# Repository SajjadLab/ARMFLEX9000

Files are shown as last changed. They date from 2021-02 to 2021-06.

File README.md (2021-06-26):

University of British Columbia  
ELEC 391

#### ARMFLEX9000
- Sajjad Al-Kazzaz
- Michael Aono
- Daniel Nadeem

# Quality Control Robot

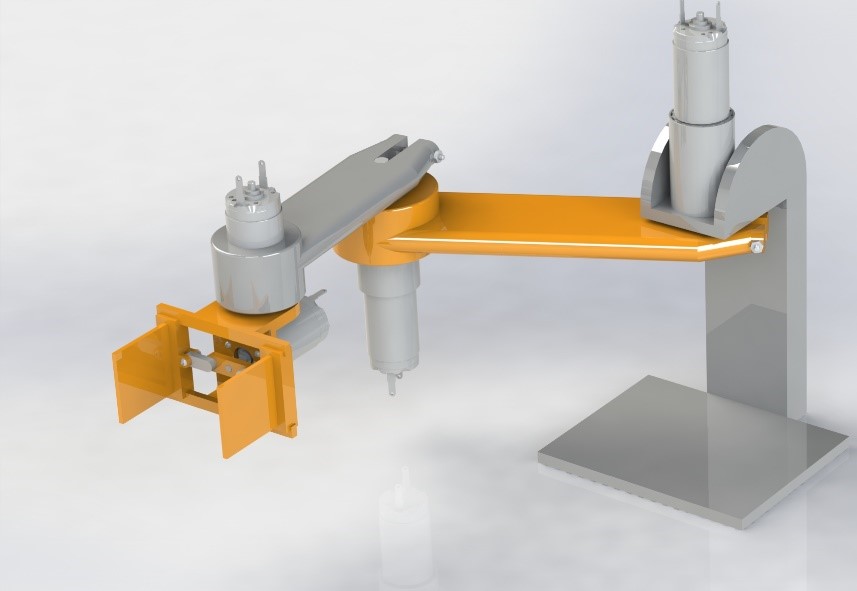
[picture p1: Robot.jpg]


[Project RCG outline](e391Proj2021.pdf)

## Project Details

## Mechanics
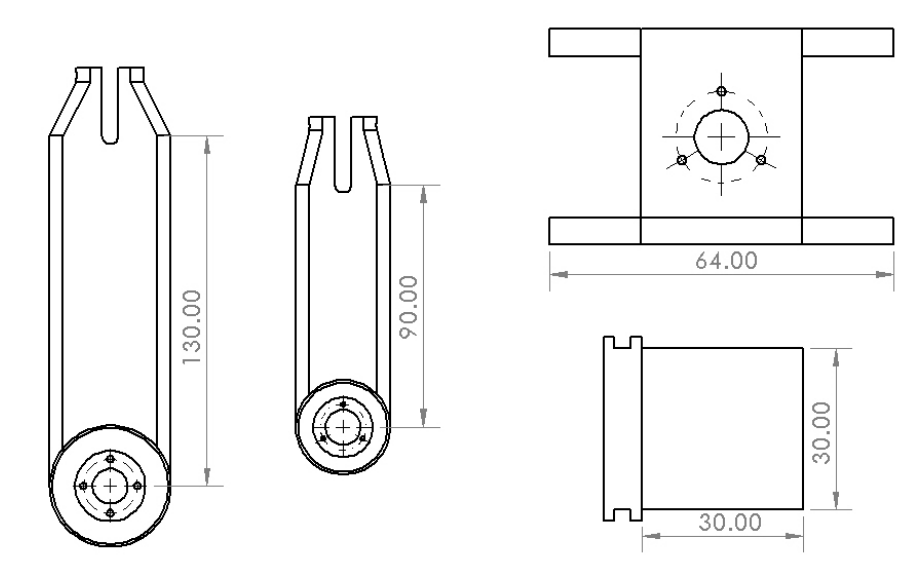
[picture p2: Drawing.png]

The physical model of a series robot arm with an attached gripping mechanism is designed and developed 
to perform quality control on marshmallows. The model is then used to find a linear approximation for 
an operating point, which is in turn used to run a simulation of the quality control procedure.

## Control
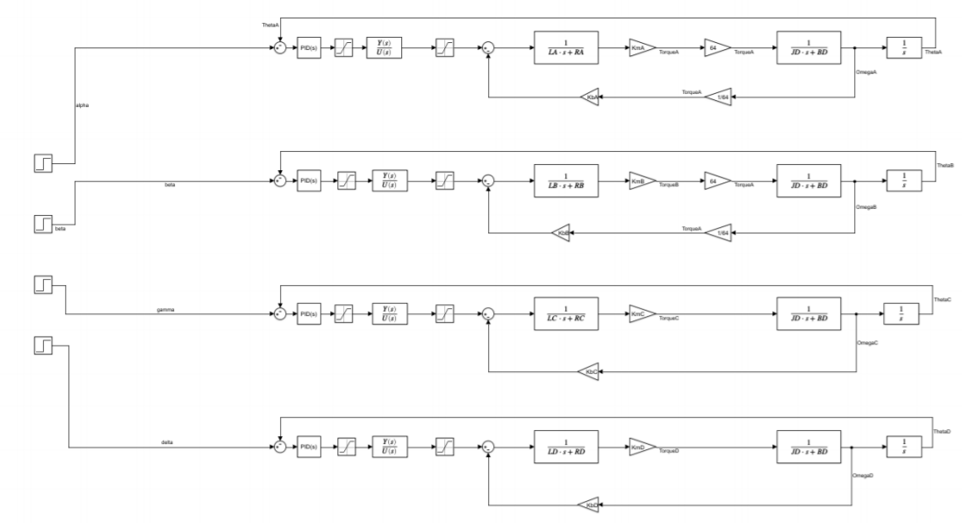
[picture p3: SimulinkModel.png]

ARMFLEX9000 is a 3.5 DOF arm that was developed for the purposes of quality
control of marshmallows on a conveyor-belt. This paper will discuss some aspects
of the design of the robot, as well as control of the robot.

In this paper, Section 1 describes the robotics, including kinematics and path
planning. Section 2 discusses robot modelling in Matlab and SimulationX.
Section 3 describes the Matlab controller, this includes system control and PID
implementation. Section 4 goes over PID tuning. Section 5 describes porting
the controller to C. Finally, Section 6 will discuss system performance.

## Electrical
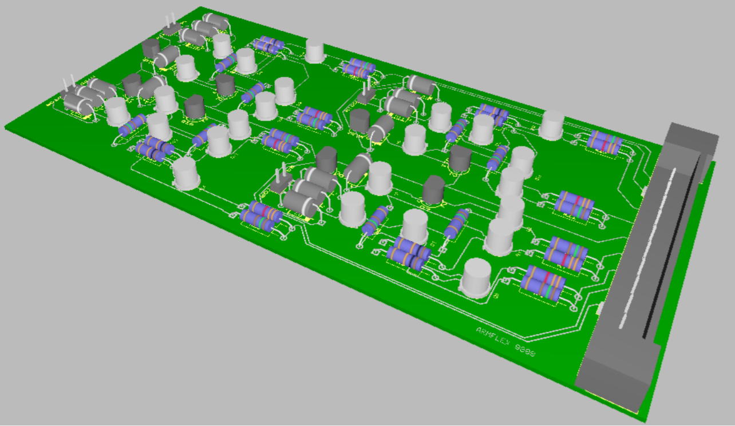
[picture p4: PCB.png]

A driver system is developed to power the motors of the quality control robot. The quality control robot
is capable of three and a half DOF and is powered by 4 identical OTS graphite communicated motors.
The torque requirements of the robot are met with the addition of planetary gear heads of reduction
ratio 64:1 on the base arms. The driver system is of H-bridge form and outputs 11.2V to the motors from
5V input. A PCD design is of the driver is developed to create a mother-daughter board with the Ardinuo
Leonardo.

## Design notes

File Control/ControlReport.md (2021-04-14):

# Quality Control System

## ARMFLEX9000
## April 4, 2021
## Sajjad Al-Kazzaz, ECE, University of British Columbia
## Vancouver, BC, Canada

\newpage

### Table of Contents

- [Abstract](#Abstract)
- [Nomenclature](#Nomenclature)
- [Robotics](#1-robotics)
	- Figure 1.1
- [Modelling](#2-modelling)
- [Controller](#3-controller)
- [Tuning](#4-tuning)
- [Port to C](#5-port-to-c)
- [Performance](#6-performance)

### Abstract

ARMFLEX9000 is a 3.5 DOF arm that was developed for the purposes of quality control of marshmallows on a conveyor-belt. This paper will discuss some aspects of the design of the robot, as well as control of the robot. 

In this paper, Section 1 describes the robotics, including kinematics and path planning. Section 2 discusses robot modelling in Matlab and SimulationX. Section 3 describes the Matlab controller, this includes system control and PID implementation. Section 4 goes over PID tuning. Section 5 describes porting the controller to C. Finally, Section 6 will discuss system performance.

### Nomenclature

- DOF: Degrees of freedom
- PID: Proportional, integral, and derivative

### 1. Robotics

The first thing that had to be done for the robotics of the machine was object placement and path planning. This is a crucial step that determines the length of the arm and thereby the inertia and motors used. The requirements dictated that there should be 3 cylindrical marshmallows on the stopped conveyor which the arm must be able to pick-up and discard. The chosen final positioning was determined with the help of the Mechanical team and optimized for the best results; this positioning is shown in figure 1.1. Given this positioning the optimal arm joint lengths were found to be:

$$r_a = 0.13m$$
$$r_b = 0.09m$$

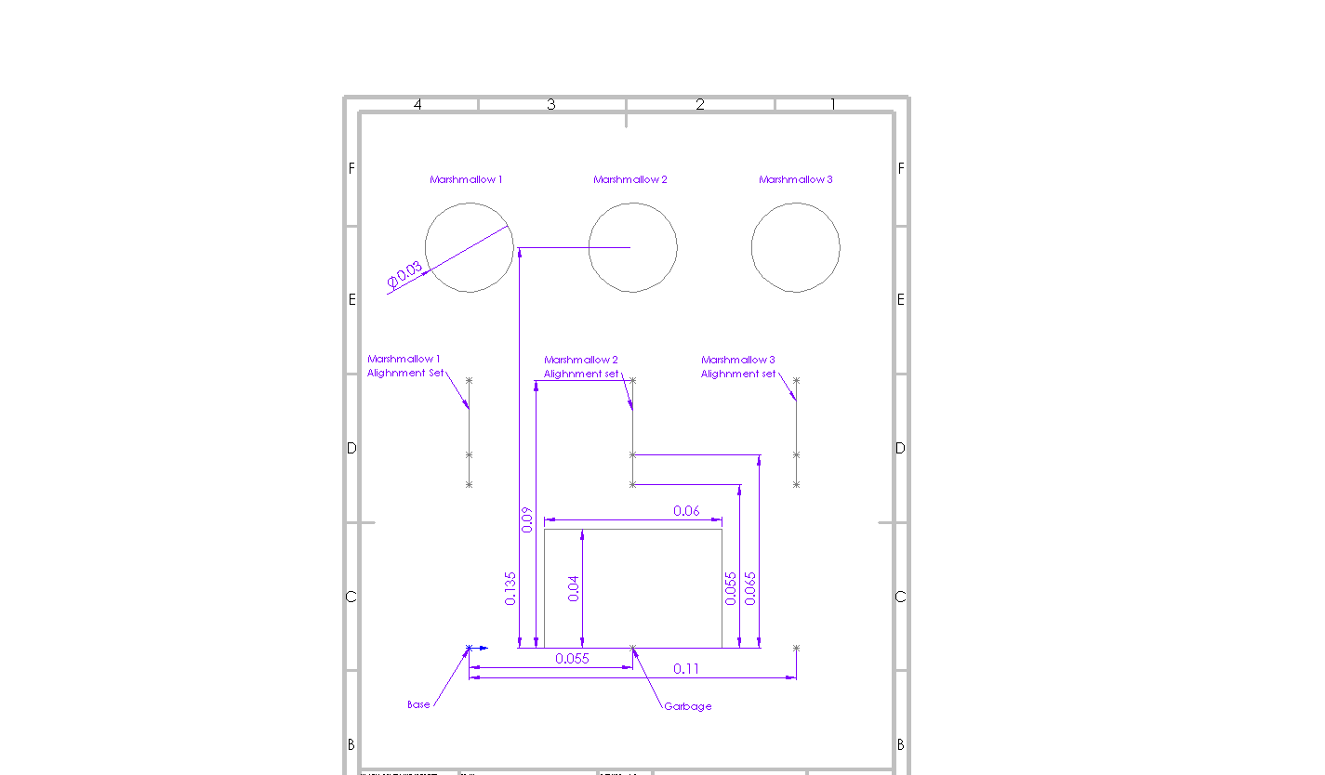
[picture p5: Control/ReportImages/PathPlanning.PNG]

*Figure 1.1*

The dots on figure 1.1 represent the path stage of the arm, to be specific the x and y coordinates of motor C. The arm starts at the calibration stage. The arm then moves to the first alignment dot, also known as the garbage dot. This is so that the arm doesn't swing and knock over marshmallows in its initial movement. The arm then follows a set of alignment dots as it approaches a specific marshmallow so that a general path can be followed that won't knock over or tip other marshmallows. Each marshmallow has its own set of alignment dots shown in the figure by a line that connects said dots. Then the arm will go to the respective pick-up dot to grab the marshmallow, followed by retracing its steps through the alignment dots and then a return to the garbage dot. From the garbage dot the controller will determine whether another marshmallow needs to be grabbed, and follow the outlined stated above, or return home and wait for further commands.

In order to translate the motor C stage coordinates into angles that can be sent to the appropriate motors, a model for inverse kinematics had to be developed. Using trigonometry the position of motor C was translated from the cartesian coordinates of the dots into polar coordinates $\alpha$ and $\beta$ for motors A and B respectively. This was done using the following formulas:

$$\beta = \arccos{\frac{x^2 + y^2 + r_a^2 + r_b^2}{2r_a r_b}}$$
$$\alpha = \arctan{\frac{y}{x}} - \arctan{\frac{r_b \sin{\beta}}{r_a + r_b \cos{\beta}}}$$

To find the necessary angle, $\gamma$, for the swivel motor C so that it remained perpendicular to the conveyor, trigonometry was also used and the following formula was calculated:
$$\gamma = \alpha + \beta - \pi/2$$

Finally, the angle $\delta$ for motor D, which controls the pincher, was found from the design of the pincher to be 0 in the release position, and $\pi/2$ in the grab position. The necessary angle $\delta$ at any time is pre-determined by the stage or dot it is in, and is part of that stages coordinates.

No forward kinematics were used in the controller since the angles were already being calculated and could be used for error calculation. Turning measured angles into measured position was unnecessary and, therefore, removed to save processing time.

### 2. Modelling

Modelling the full system was done using Simulink and SimulationX for the purposes of testing. In Simulink, 4 motor models were developed using the standard motor model and feedback systems as reference. Figure 2.1 shows the 4 motor models, each with its own feedback path. The values for the motors electrical and mechanical components were obtained from the Electrical and Mechanical teams respectively. Using this model as a blueprint, the complete model made for tuning and demoing is shown in Figure 2.2. This model replaces the mechanical components with a communication block connected to SimulationX. SimulationX does the job of more accurately calculating mechanical components and their behaviour during simulation. Figure 2.2 also shows 4 instances of the PID Matlab functions in order to meet requirements, and a central controller (on the far left) that manages overall movement of the system. In SimulationX the Mechanical team developed a simplified model of the arm using the correct weights and lengths for all the components. A Matlab transfer function block is used to model the driver circuit for each of the motors, along with saturation blocks to ensure the voltage limitations of the components aren't exceeded.

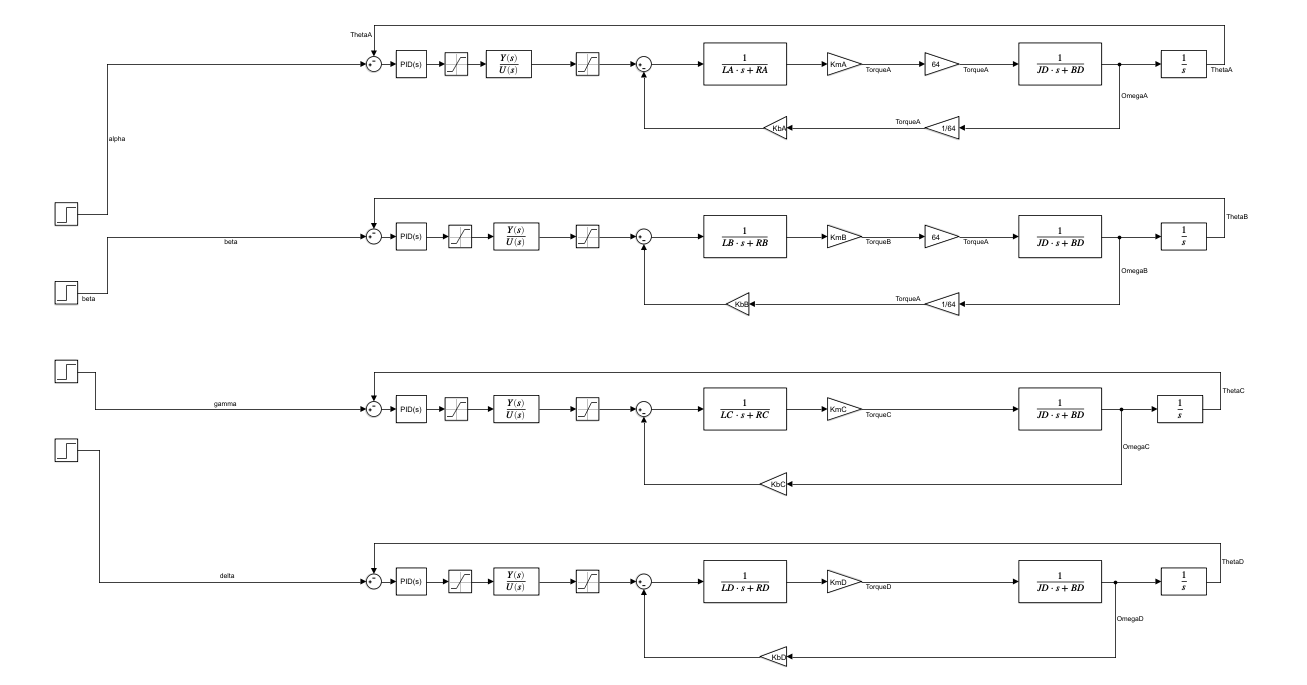
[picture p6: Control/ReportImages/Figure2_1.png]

*Figure 2.1*

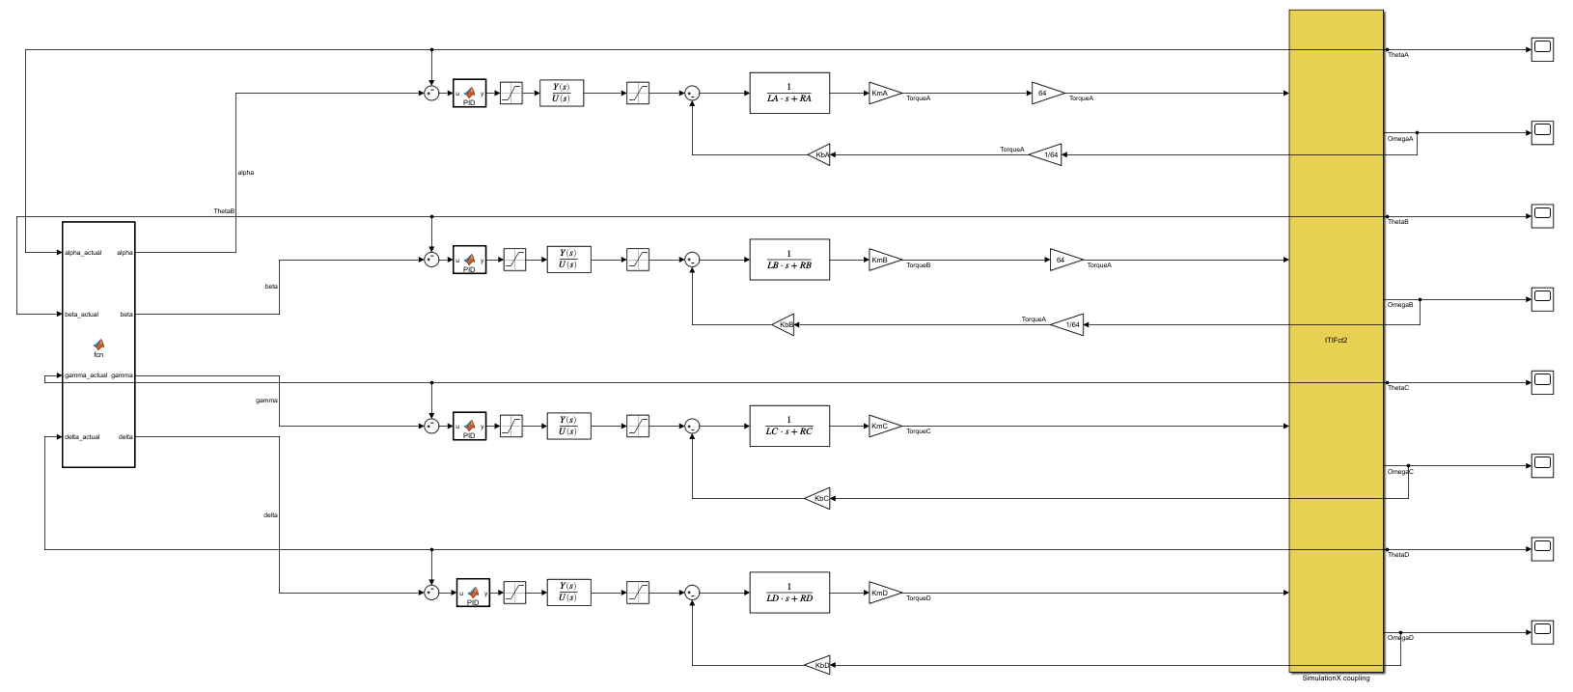
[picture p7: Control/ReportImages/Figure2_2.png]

*Figure 2.2*

### 3. Controller

There are two parts to the system control. The first is the user-defined Matlab function to replace a PID block. Figure 3.1 shows the complete code for the function. Persistent arrays and variables were used to maintain a history of previous error values for the filtered derivative and to keep track of the error sum for the integral output.

```
function y = PID(u)

persistent errorSum
persistent PrevDerivative
persistent ept
persistent Temp
Tsample = 1/500;
nhat = 16;               % Number of samples taken/kept
P = 4/(Tsample*nhat);                 % Pole
KP = 10;
KI = 5;
KD = 2;

% Initialize Temp
if isempty(Temp)
    Temp = 0;
end

% Initialize ept
if isempty(ept)
    ept = zeros(1, nhat);
    total = 0;
    for i = 1:nhat
        calc = P*exp(-P*i*Tsample);
        ept(i) = calc;
        total = total + calc;
    end
    scale = 1/(Tsample*total);
    ept = ept*scale;
end

% Initialize errorSum
if isempty(errorSum)
    errorSum = 0;
end

% Initialize PrevDerivative
if isempty(PrevDerivative)
    PrevDerivative = zeros(1,nhat);
end

% Calculate proportional output
ProportionalOutput = u*KP;

% Calculate integral output
errorSum = errorSum + u*Tsample;
IntegralOutput = errorSum*KI;

% Calculate derivative output
PrevDerivative(1) = (u - Temp);
DerivativeOutput = dot(ept, PrevDerivative)*KD;

% Take a step in time
for n = 1:(nhat - 1)
    PrevDerivative(nhat + 1 - n) = PrevDerivative(nhat - n);
end

% Update Temp
Temp = u;

% Sum all outputs and return,
y = ProportionalOutput + IntegralOutput + DerivativeOutput;
end
```
*Figure 3.1*

The second part of the system control is the system controller. This is a Matlab function that has the coordinates for all the stages relevant to each of the motors and a way of keeping track of which stage the system is in at any point in time. This controller also allows the user to choose which marshmallows to pick-up during the sequence. The complete function is shown in Figure 3.2. Each clock cycle the controller calculates the error between the desired, calculated angles and the true angles being read from SimulationX. Once the error for a particular stage drops below a threshold value, the controller considers that stage complete and increments to the next stage; if the completed stage was the last stage in a marshmallows set then the next marshmallow in the list is targeted. Once the last marshmallow in the list has finished its sequence, the controller sends the arm back to the home calibration position. 

```
function [alpha, beta, gamma, delta] = fcn(alpha_actual, beta_actual, gamma_actual, delta_actual)
% Constants
ra = 0.13;
rb = 0.09;
M1Coord = {[0.055, 0, pi/2], [0, 0.055, 0],     [0, 0.065, 0],     [0, 0.09, 0],     [0, 0.09, pi/2],     [0, 0.065, pi/2],     [0.055, 0, pi/2], [0.055, 0, 0]};
M2Coord = {[0.055, 0, pi/2], [0.055, 0.055, 0], [0.055, 0.065, 0], [0.055, 0.09, 0], [0.055, 0.09, pi/2], [0.055, 0.065, pi/2], [0.055, 0, pi/2], [0.055, 0, 0]};
M3Coord = {[0.055, 0, pi/2], [0.11, 0.055, 0],  [0.11, 0.065, 0],  [0.11, 0.09, 0],  [0.11, 0.09, pi/2],  [0.11, 0.065, pi/2], [0.055, 0, pi/2], [0.055, 0, 0]};
marshmallows = {M1Coord, M2Coord, M3Coord};

% Persistent
persistent completedMarshmallow
persistent completedStage

if isempty(completedMarshmallow)
    completedMarshmallow = 1;
end

if isempty(completedStage)
    completedStage = 1;
end

% Make sure some value exists JIC
alpha = 0;
beta = 0;
gamma = 0;
delta = 0;

% Which and how many marshmallows to grab
marshmallowGrab = [1, 2, 3];
marshmallowCount = 3;

if completedMarshmallow < marshmallowCount + 1
    % If we havent grabbed all the marshmallows then pick
    % completedMarshmallow
    currentMarshmallow = marshmallowGrab(completedMarshmallow);
    
    % Check if we have completed all stages
    if completedStage < 9
        % Set the target position
        xc = marshmallows{currentMarshmallow}{completedStage}(1);
        yc = marshmallows{currentMarshmallow}{completedStage}(2);
        delta = marshmallows{currentMarshmallow}{completedStage}(3);
    
        % Calculate required angles
        beta = acos((xc^2 + yc^2 - ra^2 - rb^2)/(2*ra*rb));

        alpha = atan(yc/xc) - atan((rb*sin(beta))/(ra + rb*cos(beta)));

        gamma = (alpha_actual + beta_actual - pi/2);
        
        % Check if we have reached target location (withing 2%)
        errorAlpha = abs(2*(alpha_actual - alpha)/(abs(alpha_actual) + abs(alpha)))
        errorBeta = abs(2*(beta_actual - beta)/(abs(beta_actual) + abs(beta)))
        errorGamma = (gamma_actual - gamma)
        errorDelta = (delta_actual - delta)
        
        if errorAlpha < 0.02 && errorBeta < 0.02 && errorGamma < 0.002 && errorDelta < 0.005
            % We have reached target position
            % Increment completedStage
            completedStage = completedStage + 1;
        end
    else
        % We have finished all stages so reset and go to next marshmallow
        completedStage = 1;
        completedMarshmallow = completedMarshmallow + 1;
    end
    
else
    % We have grabbed all marshmallow so we return to home
    alpha = 0;
    beta = 0;
    gamma = 0;
    delta = 0;
end

[alpha, beta, gamma, delta];
```
*Figure 3.2*

### 4. Tuning

To tune the system root locus and margin analysis tools were used to give a starting location. The open-loop transfer functions for each of the motors was obtained using the values and models developed in Section 2, Figure 1.2. As an estimation, the value for the controller frequency was chosen to be a very conservative 1000Hz. Thus, nhat, the number of samples used to calculate the filtered derivative, was chosen to be 10; this results in a filter pole of 400 for the purposes of testing. The root locus and margin graphs for the each of the 4 motors are shown in figures 4.1, 4.2, 4.3, and 4.4 respectively. Using this information a suitable starting location for the PID zeros was chosen for each of the motors and tested using the model from Section 2, Figure 1.3. Through trial and error each of the motors were tuned to achieve the desired results. The final PID values for all the motors are summarized in Table 1.1. 

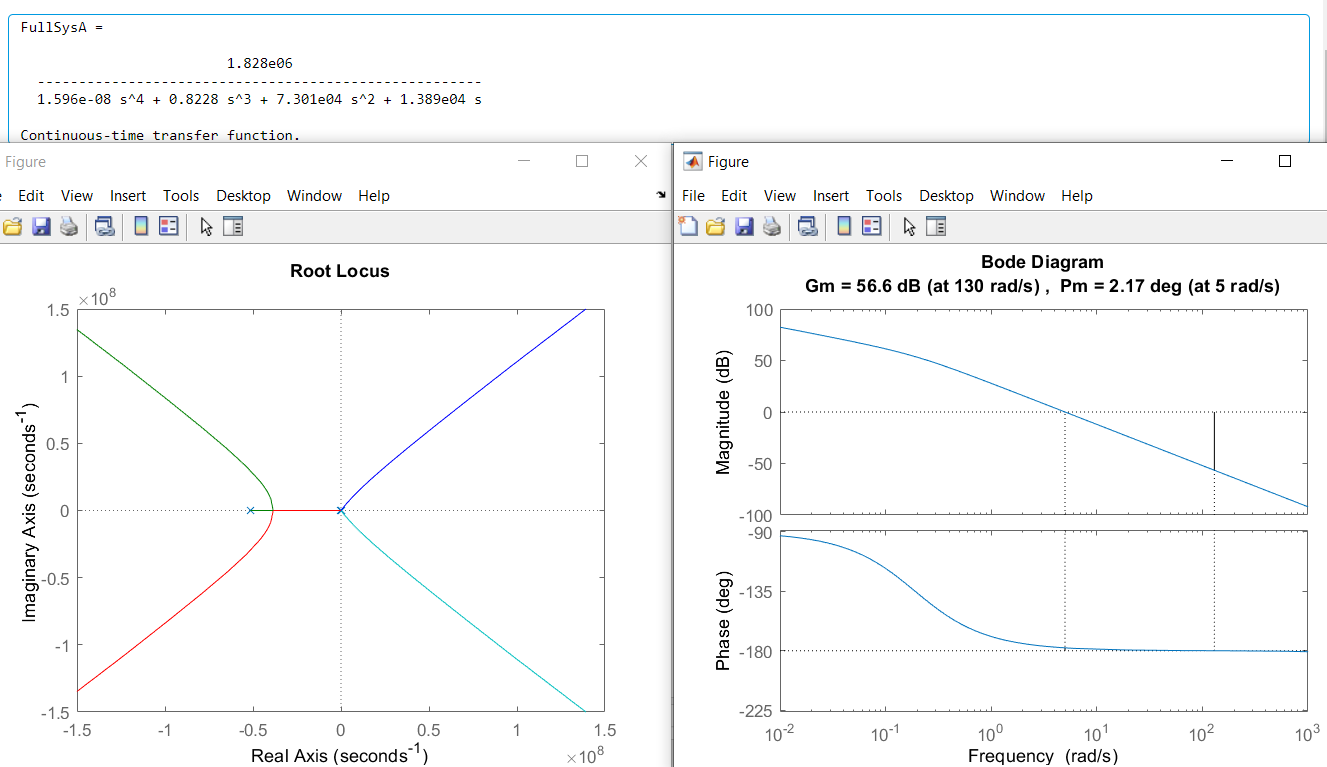
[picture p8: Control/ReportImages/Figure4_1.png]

*Figure 4.1*

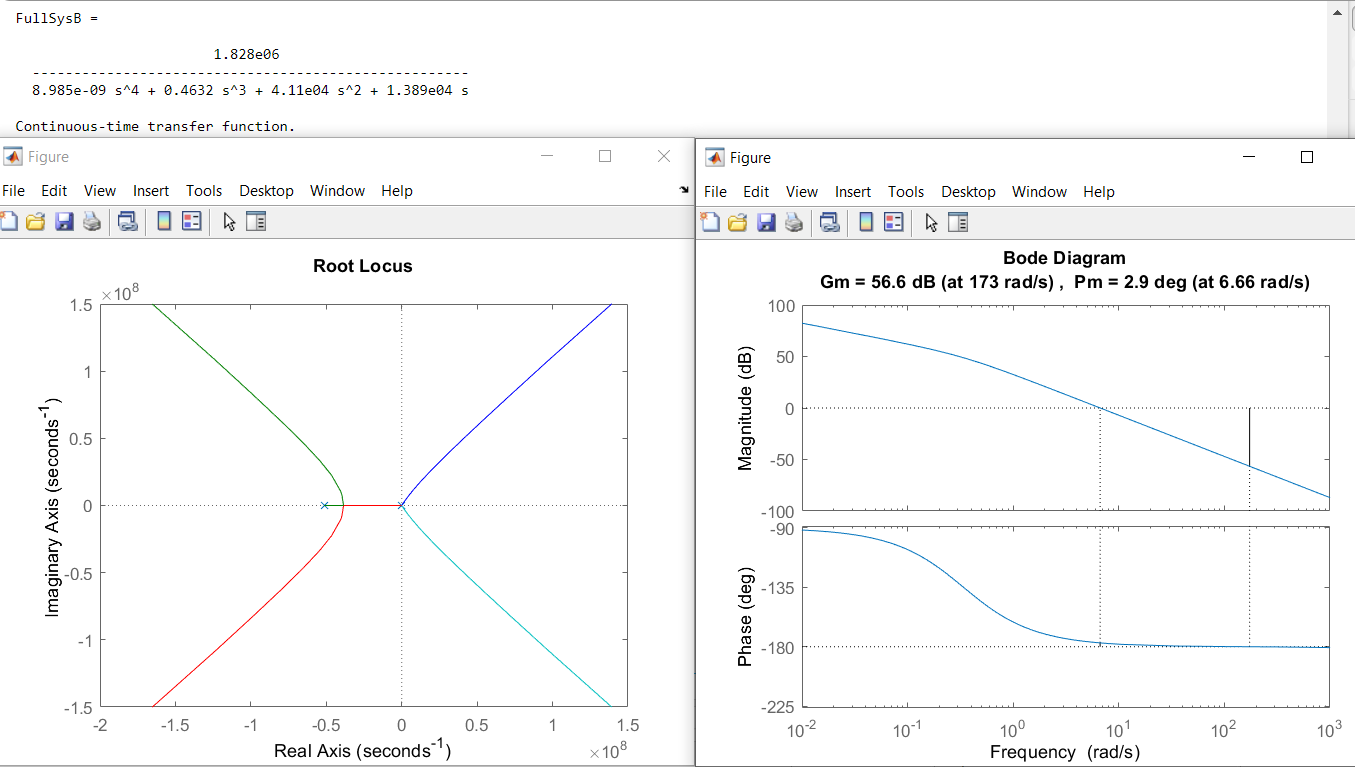
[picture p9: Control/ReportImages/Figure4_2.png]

*Figure 4.2*

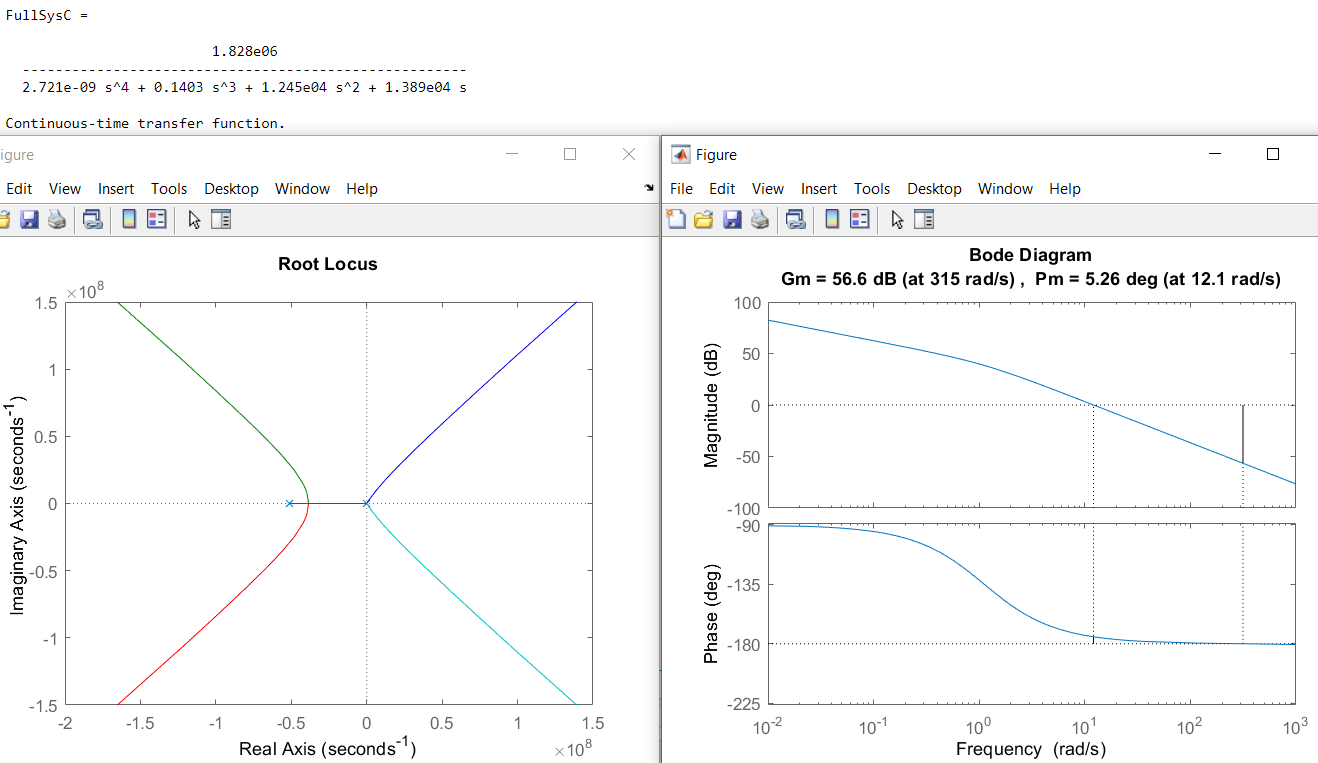
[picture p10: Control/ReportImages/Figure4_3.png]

*Figure 4.3*

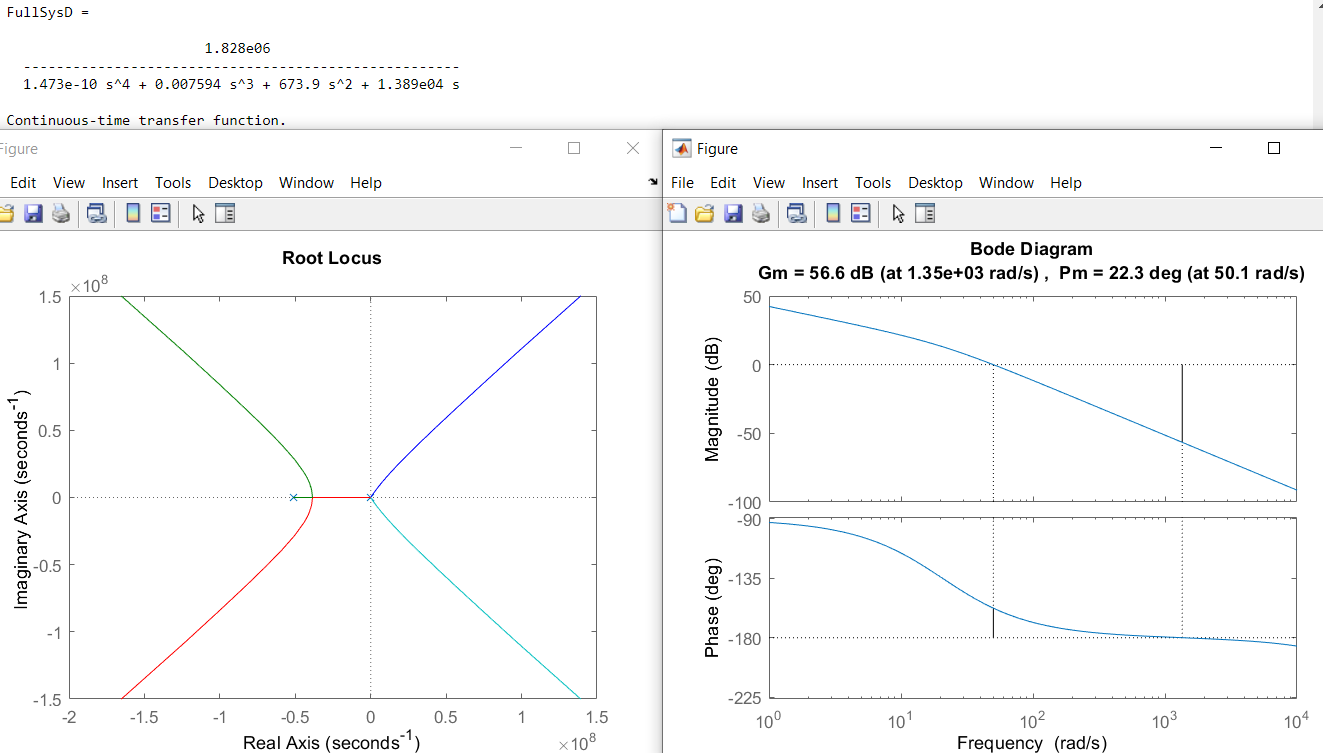
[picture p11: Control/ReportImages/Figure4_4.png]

*Figure 4.4*

*Table 1.1*

### 5. Port to C

Due to the similarities between Matlab and C porting the functions developed in Section 3 was fairly easy. Most of the code was copied straight from the Matlab functions and adjusted to meet the syntax requirements of C. Certain constants, like the arm lengths and their squares, are pre-calculated to reduce processing time. To further save processing time the array of cartesian coordinates for the stages of all the marshmallows are pre-translated to the polar coordinates for $\alpha$ and $\beta$ during setup so that these lengthy calculations aren't repeated during the actual interrupt routine. The complete arduino C code is shown in Figure 5.1.

```
#define TIMER_INTERRUPT_DEBUG 0

// Parameters:
// KP, KI, KD
double gainA[3] = {0.82, 0.008, 0.2};
double gainB[3] = {0.99, 0.01, 0.26};
double gainC[3] = {1, 0.0075, 0.2};
double gainD[3] = {2, 0.1, 0.08};
double ra = 0.13;
double rb = 0.09;
#define RaSquared 0.0169
#define RbSquared 0.0081
#define RaRb2 0.0234   // 2*ra*rb
#define HalfTurn 1.571 // Pi/2

// Timer
#define USE_TIMER_1 true
#define TIMER1_FREQ_HZ 3000

// Libraries
#include <math.h>
#include "TimerInterrupt.h"

const double Tsample = 1/3000;
const int nhat = 8;
const int P = 4/(Tsample*nhat);

// Pins:
int InputA = A1;        // Analog input pin for error
int InputB = A1;
int InputC = A1;
int InputD = A1;

int OutputA = A2;      // Analog output pin for the control signal
int OutputB = A3; 
int OutputC = A4; 
int OutputD = A6; 

// Coordinates:
double marshmallows[][8][3] = {\
{{0.055, 0, 0}, {0, 0.055, 0},     {0, 0.065, 0},     {0, 0.09, 0},     {0, 0.09, HalfTurn},     {0, 0.06, HalfTurn},     {0.055, 0, HalfTurn}, {0.055, 0, 0}}\
, {{0.055, 0, 0}, {0.055, 0.055, 0}, {0.055, 0.065, 0}, {0.055, 0.09, 0}, {0.055, 0.09, HalfTurn}, {0.055, 0.06, HalfTurn}, {0.055, 0, HalfTurn}, {0.055, 0, 0}}\
, {{0.055, 0, 0}, {0.11, 0.055, 0},  {0.11, 0.065, 0},  {0.11, 0.09, 0},  {0.11, 0.09, HalfTurn},  {0.11, 0.065, HalfTurn}, {0.055, 0, HalfTurn}, {0.055, 0, 0}}};

// Persistent:
double PrevDerivativeA[nhat] = {0};
double PrevDerivativeB[nhat] = {0};
double PrevDerivativeC[nhat] = {0};
double PrevDerivativeD[nhat] = {0};
double ept[nhat];
double Temp = 0; 
int completedMarshmallow = 0;
int completedStage = 0;
double errorSumA = 0;
double errorSumB = 0;
double errorSumC = 0;
double errorSumD = 0;

// Functions
void PID(int out, double error, double errorSum, double gain[], double PrevDerivative[]) {
  // Proportional
  double ProportionalOutput = gain[0]*error;

  // Integral
  errorSum += error*Tsample;
  double IntegralOutput = gain[1]*errorSum;

  // Filtered derivative
  PrevDerivative[0] = error - Temp;
  
  // Derivative output
  double DerivativeOutput = 0;
  // Dot product
  for(int n=0; n<nhat; n++) {
    DerivativeOutput += PrevDerivative[n]*ept[n];
  }
  
  // Shift PrevDerivative:
  for(int n=0; n<=nhat-1; n++){
    PrevDerivative[nhat + 1 - n] = PrevDerivative[nhat - n];
  }
  
  // Update Temp
  Temp = error;

  // Output
  analogWrite(out, ProportionalOutput + IntegralOutput + DerivativeOutput*gain[2]);
}

void Controller() {
  // Which and how many marshmallows are we grabbing
  int marshmallowGrab[] = {1, 2, 3};
  int marshmallowCount = 3;

  // Read values
  double alpha_actual = analogRead(InputA);
  double beta_actual = analogRead(InputB);
  double gamma_actual = analogRead(InputC);
  double delta_actual = analogRead(InputD);

  if(completedMarshmallow < marshmallowCount) {
    // If we havent grabbed all the marshmallows then pick
    // completedMarshmallow
    int currentMarshmallow = marshmallowGrab[completedMarshmallow];

    if(completedStage < 8) {
      // Set the target position
      double alpha = marshmallows[currentMarshmallow][completedStage][1];
      double beta = marshmallows[currentMarshmallow][completedStage][2];
      double delta = marshmallows[currentMarshmallow][completedStage][3];

      double gamma = (alpha_actual + beta_actual - HalfTurn);

      // Check if we have reached target location (withing 2%)
      double errorAlpha = (alpha_actual - alpha);
      double errorBeta = (beta_actual - beta);
      double errorGamma = (gamma_actual - gamma);
      double errorDelta = (delta_actual - delta);
      
      if(errorAlpha < 0.05 && errorBeta < 0.05 && errorGamma < 0.002 && errorDelta < 0.005) {
        // We have reached target position
        // Increment completedStage
        completedStage++;
      }
      else {
        PID(OutputA, errorAlpha, errorSumA, gainA, PrevDerivativeA);
        PID(OutputB, errorBeta, errorSumB, gainB, PrevDerivativeB);
        PID(OutputC, errorGamma, errorSumC, gainC, PrevDerivativeC);
        PID(OutputD, errorDelta, errorSumD, gainD, PrevDerivativeD);
      }
    }
    else {
      completedStage = 0;
      completedMarshmallow++;
    } 
  }
  else {
    // We are done grabbing, go home and callobrate
    double alpha = 0;
    double beta = 0;
    double gamma = 0;
    double delta = 0;

    // Check if we have reached target location (withing 2%)
    double errorAlpha = (alpha_actual - alpha);
    double errorBeta = (beta_actual - beta);
    double errorGamma = (gamma_actual - gamma);
    double errorDelta = (delta_actual - delta);

    // Call PID
    PID(OutputA, errorAlpha, errorSumA, gainA, PrevDerivativeA);
    PID(OutputB, errorBeta, errorSumB, gainB, PrevDerivativeB);
    PID(OutputC, errorGamma, errorSumC, gainC, PrevDerivativeC);
    PID(OutputD, errorDelta, errorSumD, gainD, PrevDerivativeD);
  }
}

void setup() {
  pinMode(InputA, INPUT);
  pinMode(InputB, INPUT);
  pinMode(InputC, INPUT);
  pinMode(InputD, INPUT);
  
  pinMode(OutputA, OUTPUT);
  pinMode(OutputB, OUTPUT);
  pinMode(OutputC, OUTPUT);
  pinMode(OutputD, OUTPUT);

  // Initialize ept
  if(ept == NULL) {
    int total = 0;
    for(int i=0; i<=nhat; i++){
      ept[i] = P*exp(-P*i*Tsample);
      total = total + ept[i];
    }
    for(int i=0; i<=nhat; i++){
      ept[i] = ept[i]*(1/(Tsample*total))*Tsample;  // Double check
    }
  }

  // Convert to polar
  // For each marshmallow
  for(int i=0; i<3;i++){
    // For each stage
    for(int j=0; j<8;j++){
      double xc = marshmallows[i][j][1];
      double yc = marshmallows[i][j][2];

      // Calculate required angles
      double beta = acos((pow(xc, 2) + pow(yc, 2) - RaSquared - RbSquared)/(RaRb2));

      double alpha = atan(yc/xc) - atan((rb*sin(beta))/(ra + rb*cos(beta)));

      // Replace xc and yc with alpha and beta
      marshmallows[i][j][1] = alpha;
      marshmallows[i][j][2] = beta;
    }
  }
  
  // Initialize interrupt on timer1
  ITimer1.init();
  if (ITimer1.attachInterrupt(TIMER1_FREQ_HZ, Controller))
    Serial.println("Starting  ITimer0 OK, millis() = " + String(millis()));
  else
    Serial.println("Can't set ITimer0. Select another freq. or timer");
}

void loop() {
}
```
*Figure 5.1*

### 6. Performance

The overall arm performance is very fast; in order to pick up all three marshmallows requires just over 10s, picking up any 2 marshmallows requires 7.5s, and picking up just one marshmallow takes 5s. Assuming the probability that any one marshmallow needs to be discarded is 50%, then the expected run time of the arm is 5.94s. Even with the speed the arm moves at there is no overshoot or tipping of any marshmallows.

The processing time of the ISR routine was calculated from the arduino code in Section 5 using the standard clock rates provided. The ISR requires 2207 clock cycles to run. The Leonardo has a clock speed of 16Mhz, therefore, after the controller can run at a maximum of 7250Hz. However, to account for possible delays and errors the controller frequency is set to 7250/2 ~ 3600Hz. The only cost involved in this part of the project is that of the arduino itself which is about $25.

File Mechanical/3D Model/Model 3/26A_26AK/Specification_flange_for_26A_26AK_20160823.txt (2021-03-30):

Gearhead 26/A requires also a specific flange, as per combination with following motors:

2232U...SR
please add 3D - file name: 26A_flange_a

(c) Copyright 2019, DR.FRITZ FAULHABER GMBH & CO.KG.
All rights reserved.

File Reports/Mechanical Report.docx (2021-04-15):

# Quality Control Robot - Mechanics

April 14, 2021

Daniel Nadeem, ECE, UBC, Vancouver, BC, Canada

Abstract

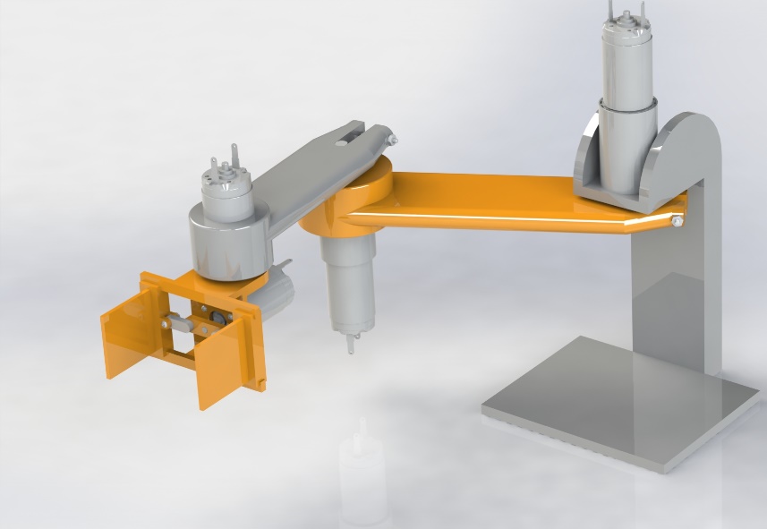
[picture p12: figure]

The physical model of a series robot arm with an attached gripping mechanism is designed and developed to perform quality control on marshmallows. The model is then used to find a linear approximation for an operating point, which is in turn used to run a simulation of the quality control procedure.

Figure 1: Quality Control Robot

The physical model development and analysis is as follows; Section 1 describes the 3D design of the robot including manufacturability. Section 2 describes the method in which the linear model was approximated. Section 3 goes through the stress analysis for determining possible failing points of the robot. Section 4 describes the SimulationX model including methods used to optimize simulation time.

1. 3D Design

The physical model consists of two arm segments, a wrist joint, and a linear gripping mechanism, totaling to 3.5 degrees of freedom. The first and second arm segments are 130mm and 90mm in length, respectively. The gripper claws are square with side lengths of 30mm to match the approximate size of each marshmallow. This can be seen in Figure 2.

All off-the-shelf components come from either the Faulhaber or McMaster-Carr catalogues. These components include four motor/encoder combinations, two of which contain gearheads. As well, fasteners including nuts and bolts are used to secure the robot’s parts together. The remaining custom parts can be 3D printed from ABS plastic. These parts include the first and second arm segments, the gripper base, the two claws, and the gripping linkages.

The robot’s mounting post is designed to route wires up from the base plate, to each of the four motors along the length of the arm. The base plate serves as a housing for the electronics since the space directly above it does not conflict with the path of the robot.


Figure 2: Custom ABS Parts

2. Linear Model

The linear model of the robot is determined using the Mass Properties tool in SolidWorks. The moment of inertia for each of the three motors that control the arm movement, is found by removing the preceding components, then placing the axis of rotation at the origin, and then analyzing the mass properties. For example, the linear model for the second arm motor was found as follows:

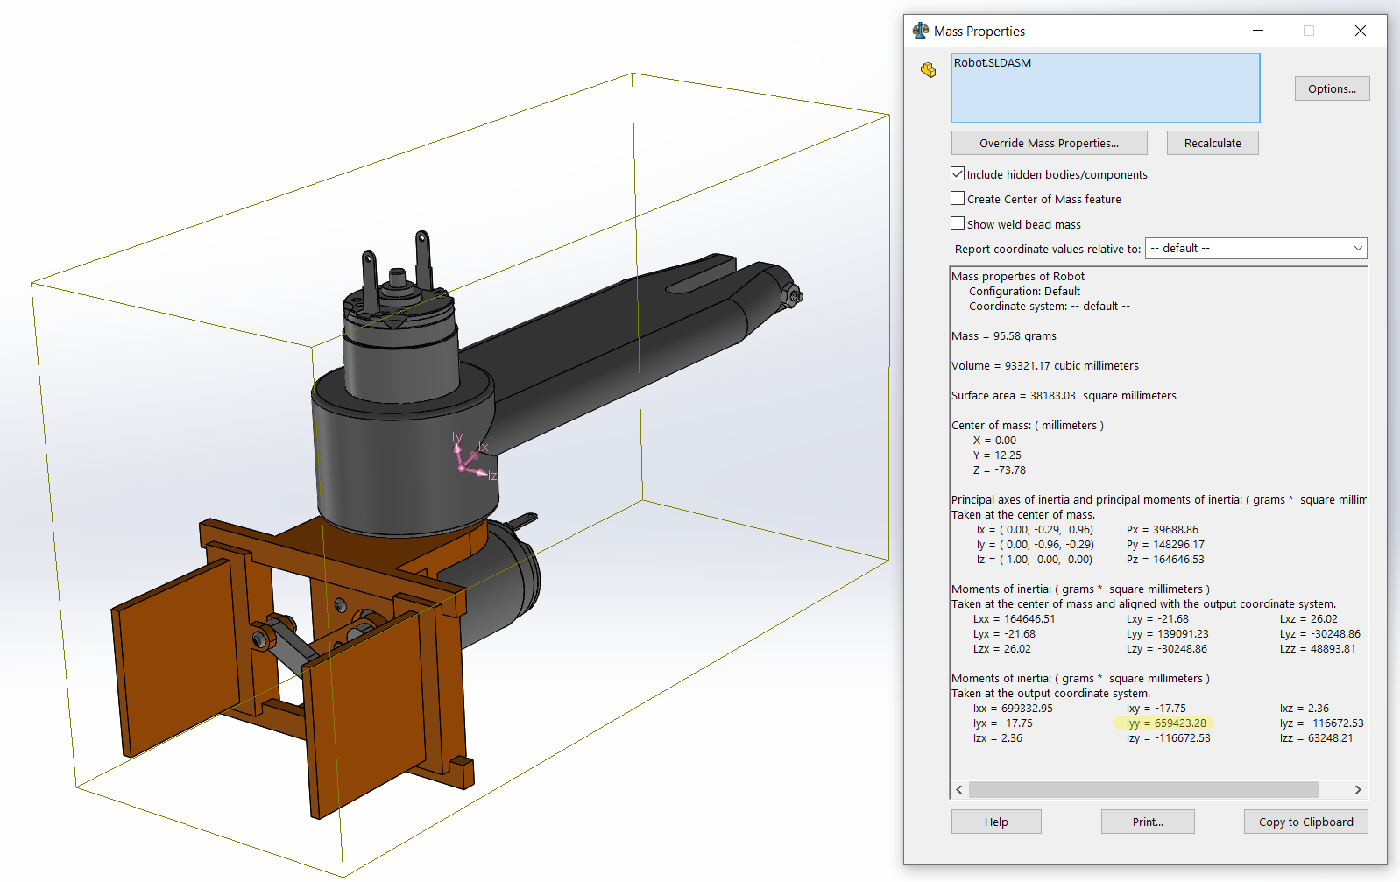
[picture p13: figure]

Figure 3: Mass Analysis

The moment of inertia experienced by the second motor is 0.659 g∙m^2 which is the inertia about the y-axis; the axis of rotation of the second motor. The value for rotational friction is taken from the datasheet of the motor.

3. Stress Analysis

To prevent any failure of the robot’s components in practice, the likely points of stress undergo a simulated test. Of the two arm segments, the maximum potential torque of the motor/gearhead combinations will occur from the second motor as it has the least inertia to move. Of the gripping mechanism parts, the maximum potential force will occur against the claws.

Depicted below are stress tests of the above-mentioned components. In both cases of maximum stress, neither part reaches the breaking point of ABS plastic.

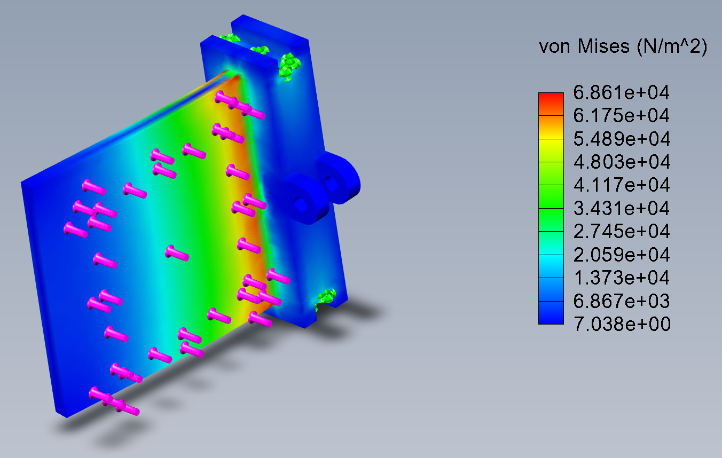
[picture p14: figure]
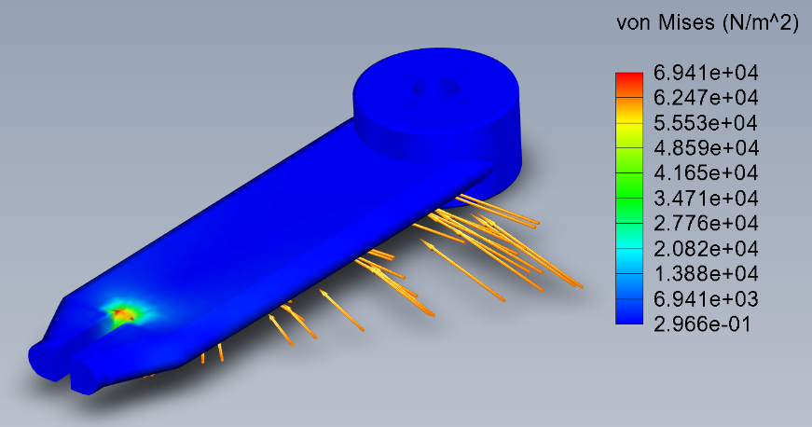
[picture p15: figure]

Figure 4: Claw Stress Analysis

Figure 5: Arm Segment Stress Analysis

4. SimulationX Model

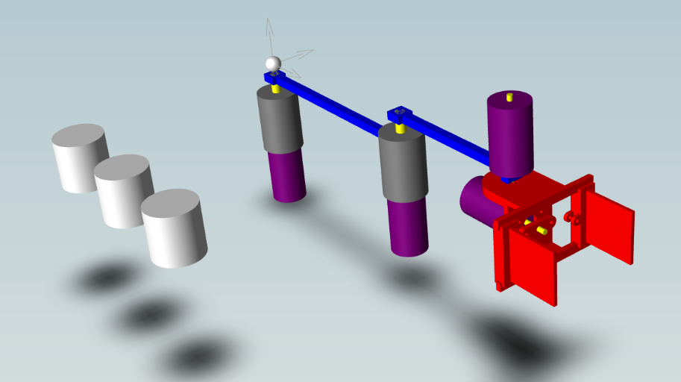
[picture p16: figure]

The linear model that was determined earlier is not accurate enough to serve as a final simulation model, whereas a SimulationX model will suffice. The simulation time of the model is optimized by limiting most of the components to primitive shapes and omitting certain functions of the gripping mechanism.

All of the motors are represented by combinations of cylinders and joint blocks. As well, rather than implementing gears within the simulation, the gain of the gearheads is represented in the Simulink control model. The arm segments are represented by rectangular prisms of the same length and mass as the 3D model’s segments.

In order to greatly limit simulation time, the gripping mechanism is reduced to a single rotating component that is directly attached to the motor’s shaft. The claws are held in a fixed position. Since the gripping mechanism requires no feedback control, but a more primitive on/off control, this omission does not affect the accuracy of the control model.

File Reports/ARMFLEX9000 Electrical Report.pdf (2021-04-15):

## Virtual Quality Control Robot Electrical System

## White-Paper Updated – April 12, 2021

ARMFLEX 9000 team member, Michael Aono, University of British Columbia, Vancouver, BC

Table of Contents

- Abstract
- Nomenclature
- Motor Selection
- Driver Design
- Figure 2.1
- Linear Modeling
- Figure 3.1
- Figure 3.2
- PCB Design
- Figure 4.1
- Figure 4.2
- Figure 4.3
- Data Sheet Reference

Abstract

A driver system is developed to power the motors of the quality control robot. The quality control robot is capable of three and a half DOF and is powered by 4 identical OTS graphite communicated motors. The torque requirements of the robot are met with the addition of planetary gear heads of reduction ratio 64:1 on the base arms. The driver system is of H-bridge form and outputs 11.2V to the motors from 5V input. A PCD design is of the driver is developed to create a mother-daughter board with the Ardinuo Leonardo.

In this paper, Section on describes motor selection. Section 2 describes driver design. Section 3 describes linear modeling of the drivers. Section 4 describes PCB layout of the design. Section 5 describes the datasheets of our motor parts.

Nomenclature

DOF | Degrees of Freedom
OTS | Off-the-shelf
PCB | Printed Circuit Board
V | Voltage
K | Gain
A | Inverse Time Constant
CM | Centimeters
CAD | Computer-aided Design

### 1. Motor Selection

The motor selection is restricted to mechanically communicated Maxon and Faulhaber products. Included in the motor selection is the optical encoder and gearheads to meet the minimum torque requirements. The motor parts are selected with the goal of minimal weight and cost. All parts are selected from Faulhaber. The Series 2237-012-CXR with graphite commutation is selected for the motors, the Series IER3-10000 L is chosen for the optical encoders, and the 2 Series 26A planetary gear heads with a 64:1 reduction ratio are used for the base arms. The total cost for the motor parts comes to $1301.25 CAD (1041.62USD).

### 2. Driver Design

The motor drivers are designed in a H-bridge formation. The driver is constraint to supplying the motor with a voltage at or below the nominal voltage. The motor is rated for a nominal voltage of 12V. An input of 5V from the Arduino Leonardo, outputs 11.2V to the motor. The design of the driver is shown in Figure 2.1.

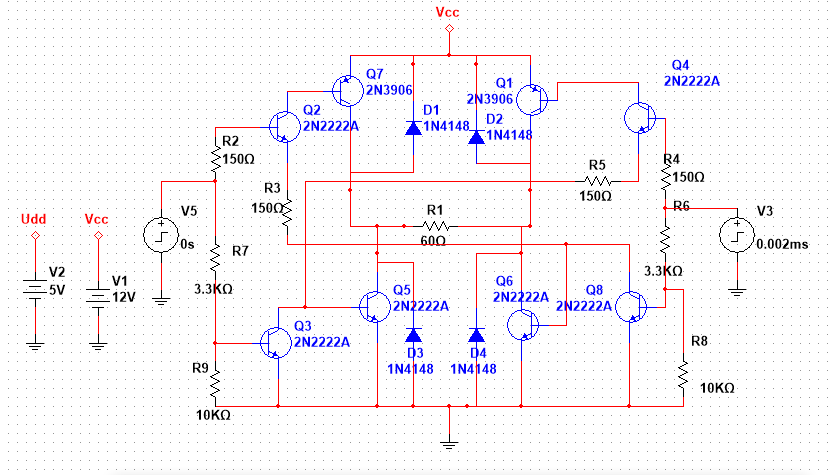
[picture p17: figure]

Figure 2.1

### 3. Linear Modeling

The driver’s step response given by Multisim is shown in Figure 3.1. Using the formula K*(A/s+A) the driver can be modeled as a first order transfer function. Using the step function in MATLAB and multiplying the input by 5 leads to an accurate model of the driver. This is shown in Figure 3.2.

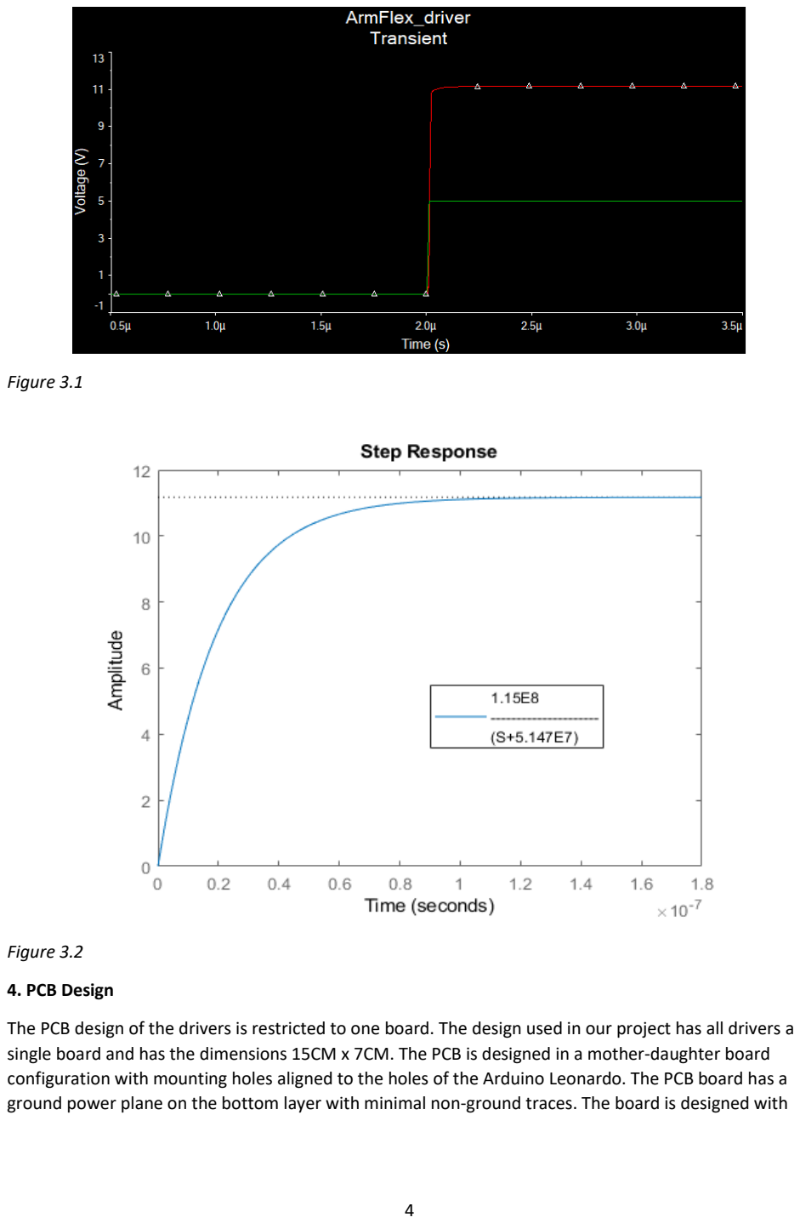
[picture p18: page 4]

Figure 3.1

Figure 3.2

### 4. PCB Design

The PCB design of the drivers is restricted to one board. The design used in our project has all drivers a single board and has the dimensions 15CM x 7CM. The PCB is designed in a mother-daughter board configuration with mounting holes aligned to the holes of the Arduino Leonardo. The PCB board has a ground power plane on the bottom layer with minimal non-ground traces. The board is designed with

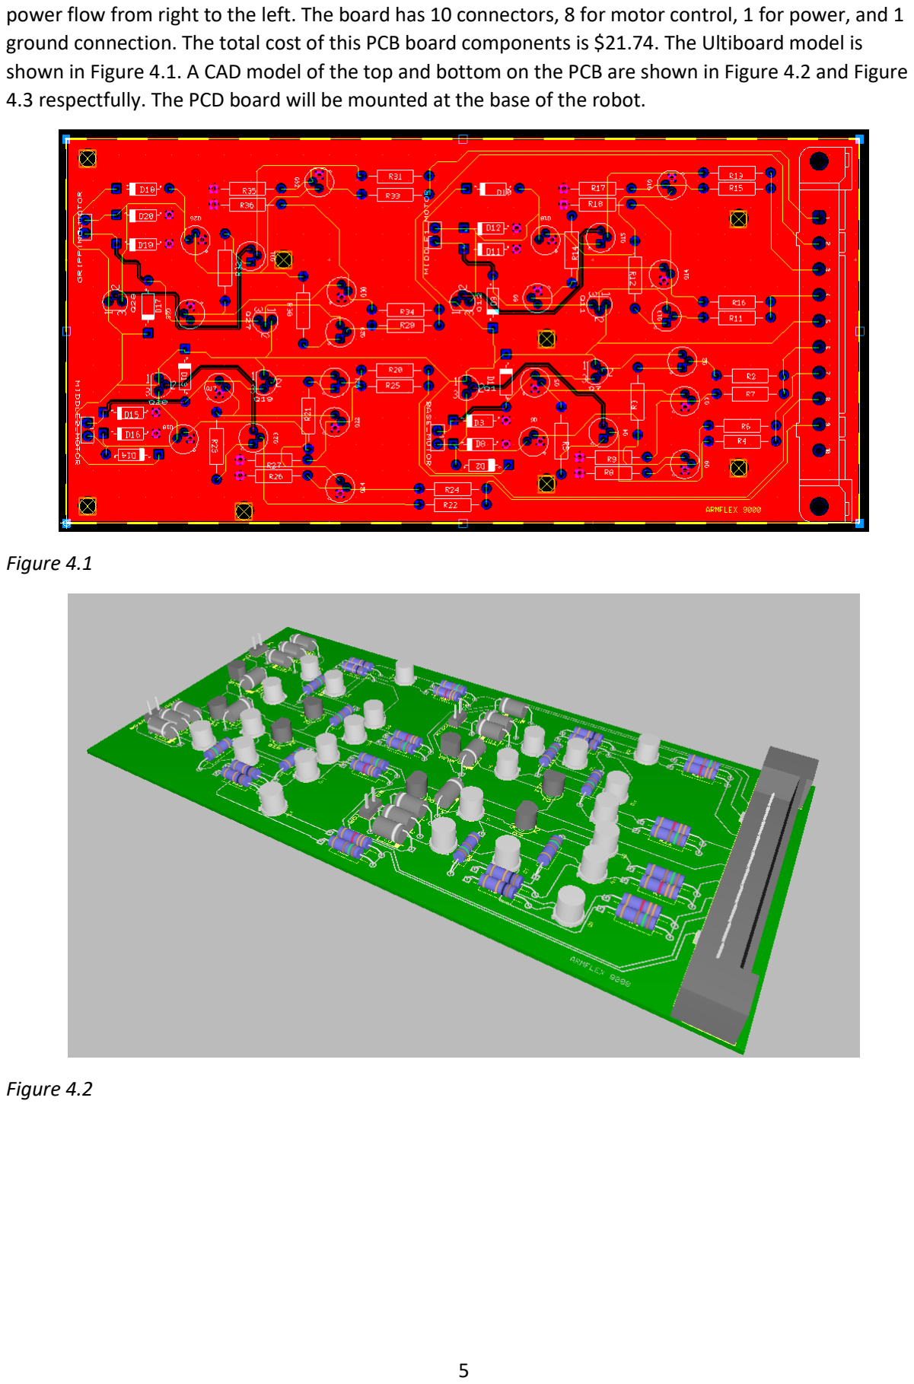
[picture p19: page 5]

power flow from right to the left. The board has 10 connectors, 8 for motor control, 1 for power, and 1 ground connection. The total cost of this PCB board components is $21.74. The Ultiboard model is shown in Figure 4.1. A CAD model of the top and bottom on the PCB are shown in Figure 4.2 and Figure 4.3 respectfully. The PCD board will be mounted at the base of the robot.

Figure 4.1

Figure 4.2

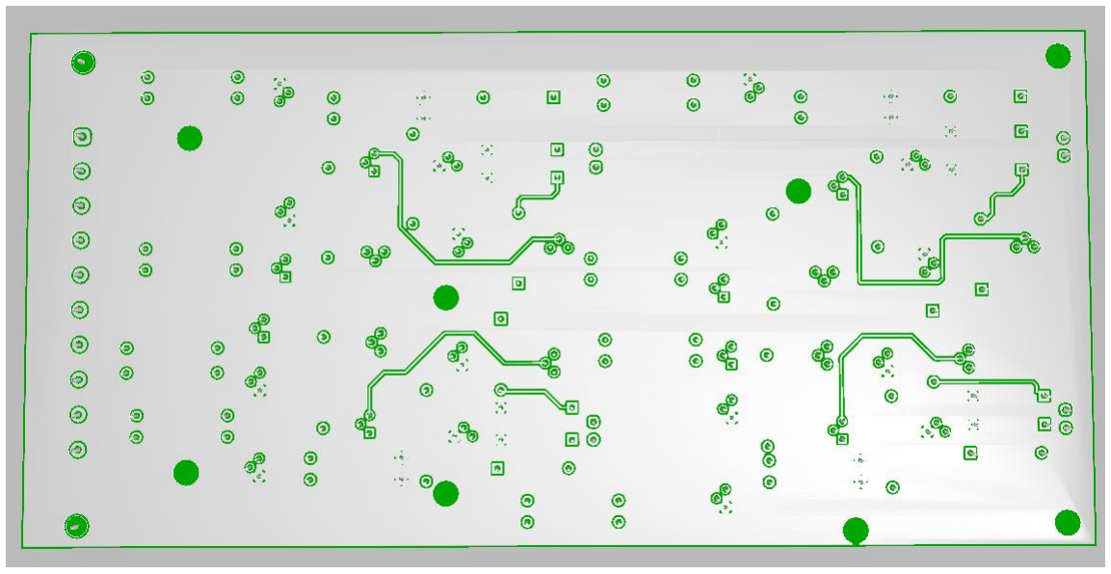
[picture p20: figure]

Figure 4.3

### 5. Data Sheets

The datasheets of the motor, encoder, and gearheads are attached with this submitted document.

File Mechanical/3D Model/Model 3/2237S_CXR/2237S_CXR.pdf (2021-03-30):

If you see this message, please change

"Comments and Forms" from Print Dialog to

"Document and Markups"

Explode / Move Parts

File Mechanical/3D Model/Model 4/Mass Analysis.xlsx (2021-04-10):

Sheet: Linear Model
 |  |  | Taken From Datasheet
Motor | J (kg*m^2) | B (N*m*s/rad) | Kt (N*m/A) | No Load Current | No Load Speed | Rotor Inertia (kg*m^2)
BaseArmMotor | 0.00010640038 | 1.295053134e-06 | 0.0159 | 0.058 | 6800 | 3.1e-07
ForeArmMotor | 5.993756e-05 | 1.295053134e-06 | 0.0159 | 0.058 | 6800
GripperMotor | 1.814061e-05 | 1.295053134e-06 | 0.0159 | 0.058 | 6800
PincherMotor |  | 1.295053134e-06 | 0.0159 | 0.058 | 6800

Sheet: BaseArmMotor
BaseArmMotor Inertia:
106400.38 | gmm^2
Mass properties of Robot
Configuration: Default
Coordinate system: -- default --
Mass = 212.28 grams
Volume = 208374.26 cubic millimeters
Surface area = 70692.90 square millimeters
Center of mass: ( millimeters )
 | X = 0.11
 | Y = 1.03
 | Z = -142.01
Principal axes of inertia and principal moments of inertia: ( grams * square millimeters )
Taken at the center of mass.
 | Ix = ( 0.00, -0.04, 1.00) | Px = 104847.84
 | Iy = ( 0.00, -1.00, -0.04) | Py = 1086847.99
 | Iz = ( 1.00, 0.00, 0.00) | Pz = 1148142.16
Moments of inertia: ( grams * square millimeters )
Taken at the center of mass and aligned with the output coordinate system.
 | Lxx = 1148138.92 | Lxy = 125.03 | Lxz = -1818.95
 | Lyx = 125.03 | Lyy = 1085524.93 | Lyz = -36021.50
 | Lzx = -1818.95 | Lzy = -36021.50 | Lzz = 106174.14
Moments of inertia: ( grams * square millimeters )
Taken at the output coordinate system.
 | Ixx = 5429475.12 | Ixy = 149.34 | Ixz = -5181.97
 | Iyx = 149.34 | Iyy = 5366640.18 | Iyz = -66960.50
 | Izx = -5181.97 | Izy = -66960.50 | Izz = 106400.38
 |  | For Calculations: | 7

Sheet: ForeArmMotor
BaseArmMotor Inertia:
59937.56 | gmm^2
Mass properties of Robot
Configuration: Default
Coordinate system: -- default --
Mass = 95.42 grams
Volume = 93155.76 cubic millimeters
Surface area = 37034.39 square millimeters
Center of mass: ( millimeters )
 | X = 0.00
 | Y = 12.23
 | Z = -73.77
Principal axes of inertia and principal moments of inertia: ( grams * square millimeters )
Taken at the center of mass.
 | Ix = ( 0.00, -0.29, 0.96) | Px = 36499.33
 | Iy = ( 0.00, -0.96, -0.29) | Py = 144669.60
 | Iz = ( 1.00, 0.00, 0.00) | Pz = 164192.56
Moments of inertia: ( grams * square millimeters )
Taken at the center of mass and aligned with the output coordinate system.
 | Lxx = 164192.56 | Lxy = -8.30 | Lxz = -0.11
 | Lyx = -8.30 | Lyy = 135504.80 | Lyz = -30122.51
 | Lzx = -0.11 | Lzy = -30122.51 | Lzz = 45664.13
Moments of inertia: ( grams * square millimeters )
Taken at the output coordinate system.
 | Ixx = 697698.53 | Ixy = -7.71 | Ixz = -3.64
 | Iyx = -7.71 | Iyy = 654737.34 | Iyz = -116211.01
 | Izx = -3.64 | Izy = -116211.01 | Izz = 59937.56
 |  | For Calculations: | 7

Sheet: GripperMotor
BaseArmMotor Inertia:
18140.61 | gmm^2
Mass properties of Robot
Configuration: Default
Coordinate system: -- default --
Mass = 34.70 grams
Volume = 33352.03 cubic millimeters
Surface area = 19110.79 square millimeters
Center of mass: ( millimeters )
 | X = 0.00
 | Y = 18.26
 | Z = -8.60
Principal axes of inertia and principal moments of inertia: ( grams * square millimeters )
Taken at the center of mass.
 | Ix = ( 0.00, -0.07, 1.00) | Px = 6536.35
 | Iy = (-0.01, -1.00, -0.07) | Py = 15463.26
 | Iz = ( 1.00, -0.01, 0.00) | Pz = 16557.54
Moments of inertia: ( grams * square millimeters )
Taken at the center of mass and aligned with the output coordinate system.
 | Lxx = 16557.41 | Lxy = 11.67 | Lxz = 0.81
 | Lyx = 11.67 | Lyy = 15424.27 | Lyz = -589.63
 | Lzx = 0.81 | Lzy = -589.63 | Lzz = 6575.47
Moments of inertia: ( grams * square millimeters )
Taken at the output coordinate system.
 | Ixx = 30689.32 | Ixy = 12.10 | Ixz = 0.61
 | Iyx = 12.10 | Iyy = 17991.03 | Iyz = -6038.03
 | Izx = 0.61 | Izy = -6038.03 | Izz = 18140.61
 |  | For Calculations: | 7

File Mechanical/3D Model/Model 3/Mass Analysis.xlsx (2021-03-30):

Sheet: Analysis
 |  |  | Taken From Datasheet
Motor | J (kg*m^2) | B (N*m*s/rad) | Kt (N*m/A) | No Load Current | No Load Speed | Rotor Inertia (kg*m^2)
BaseArmMotor | 0.00012770002 | 1.295053134e-06 | 0.0159 | 0.058 | 6800 | 3.1e-07
ForeArmMotor | 3.922709e-05 | 1.295053134e-06 | 0.0159 | 0.058 | 6800
GripperMotor | 1.814061e-05 | 1.295053134e-06 | 0.0159 | 0.058 | 6800
PincherMotor |  | 1.295053134e-06 | 0.0159 | 0.058 | 6800

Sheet: BaseArmMotor
BaseArmMotor Inertia:
127700.02 | gmm^2
Mass properties of Robot
Configuration: Default
Coordinate system: -- default --
Mass = 141.25 grams
Volume = 136014.84 cubic millimeters
Surface area = 61942.41 square millimeters
Center of mass: ( millimeters )
 | X = 0.29
 | Y = 3.75
 | Z = -155.40
Principal axes of inertia and principal moments of inertia: ( grams * square millimeters )
Taken at the center of mass.
 | Ix = ( 0.00, -0.20, 0.98) | Px = 101844.56
 | Iy = ( 0.00, -0.98, -0.20) | Py = 712421.86
 | Iz = ( 1.00, 0.00, 0.00) | Pz = 790727.33
Moments of inertia: ( grams * square millimeters )
Taken at the center of mass and aligned with the output coordinate system.
 | Lxx = 790715.43 | Lxy = 772.32 | Lxz = -2682.59
 | Lyx = 772.32 | Lyy = 688571.41 | Lyz = -118295.46
 | Lzx = -2682.59 | Lzy = -118295.46 | Lzz = 125706.90
Moments of inertia: ( grams * square millimeters )
Taken at the output coordinate system.
 | Ixx = 4203636.54 | Ixy = 923.11 | Ixz = -8938.50
 | Iyx = 923.11 | Iyy = 4099522.35 | Iyz = -200510.35
 | Izx = -8938.50 | Izy = -200510.35 | Izz = 127700.02
 |  | For Calculations: | 7

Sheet: ForeArmMotor
BaseArmMotor Inertia:
39227.09 | gmm^2
Mass properties of Robot
Configuration: Default
Coordinate system: -- default --
Mass = 74.44 grams
Volume = 71418.77 cubic millimeters
Surface area = 34731.36 square millimeters
Center of mass: ( millimeters )
 | X = 0.00
 | Y = 9.24
 | Z = -78.32
Principal axes of inertia and principal moments of inertia: ( grams * square millimeters )
Taken at the center of mass.
 | Ix = ( 0.00, -0.20, 0.98) | Px = 30157.15
 | Iy = ( 0.00, -0.98, -0.20) | Py = 98878.06
 | Iz = ( 1.00, 0.00, 0.00) | Pz = 116463.81
Moments of inertia: ( grams * square millimeters )
Taken at the center of mass and aligned with the output coordinate system.
 | Lxx = 116463.79 | Lxy = 16.91 | Lxz = -10.06
 | Lyx = 16.91 | Lyy = 96166.53 | Lyz = -13378.61
 | Lzx = -10.06 | Lzy = -13378.61 | Lzz = 32868.69
Moments of inertia: ( grams * square millimeters )
Taken at the output coordinate system.
 | Ixx = 579477.00 | Ixy = 14.66 | Ixz = 9.02
 | Iyx = 14.66 | Iyy = 552821.33 | Iyz = -67263.60
 | Izx = 9.02 | Izy = -67263.60 | Izz = 39227.09
 |  | For Calculations: | 7

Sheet: GripperMotor
BaseArmMotor Inertia:
18140.61 | gmm^2
Mass properties of Robot
Configuration: Default
Coordinate system: -- default --
Mass = 34.70 grams
Volume = 33352.03 cubic millimeters
Surface area = 19110.79 square millimeters
Center of mass: ( millimeters )
 | X = 0.00
 | Y = 18.26
 | Z = -8.60
Principal axes of inertia and principal moments of inertia: ( grams * square millimeters )
Taken at the center of mass.
 | Ix = ( 0.00, -0.07, 1.00) | Px = 6536.35
 | Iy = (-0.01, -1.00, -0.07) | Py = 15463.26
 | Iz = ( 1.00, -0.01, 0.00) | Pz = 16557.54
Moments of inertia: ( grams * square millimeters )
Taken at the center of mass and aligned with the output coordinate system.
 | Lxx = 16557.41 | Lxy = 11.67 | Lxz = 0.81
 | Lyx = 11.67 | Lyy = 15424.27 | Lyz = -589.63
 | Lzx = 0.81 | Lzy = -589.63 | Lzz = 6575.47
Moments of inertia: ( grams * square millimeters )
Taken at the output coordinate system.
 | Ixx = 30689.32 | Ixy = 12.10 | Ixz = 0.61
 | Iyx = 12.10 | Iyy = 17991.03 | Iyz = -6038.03
 | Izx = 0.61 | Izy = -6038.03 | Izz = 18140.61
 |  | For Calculations: | 7

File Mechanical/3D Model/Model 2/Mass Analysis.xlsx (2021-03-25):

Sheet: Analysis
Motor | J (g*mm^2) | B (m*Nm)
BaseArmMotor | Iyy = 1604720.43 | 0.08 | Rotor Inertia (g*mm^2)
ForeArmMotor | Izz = 24796.61 | 0.08 | 68
GripperMotor | Ixx = 21422.46 | 0.08
PincherMotor |  | 0.08

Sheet: BaseArmMotor
Mass properties of Robot
Configuration: Default
Coordinate system: -- default --
Mass = 89.53 grams
Volume = 84705.90 cubic millimeters
Surface area = 48550.63 square millimeters
Center of mass: ( millimeters )
 | X = -26.85
 | Y = 15.20
 | Z = -113.59
Principal axes of inertia and principal moments of inertia: ( grams * square millimeters )
Taken at the center of mass.
 | Ix = (-0.18, -0.18, 0.97) | Px = 83808.65
 | Iy = ( 0.97, 0.13, 0.20) | Py = 326016.31
 | Iz = (-0.16, 0.98, 0.15) | Pz = 395954.44
Moments of inertia: ( grams * square millimeters )
Taken at the center of mass and aligned with the output coordinate system.
 | Lxx = 320180.99 | Lxy = 18533.50 | Lxz = -39900.58
 | Lyx = 18533.50 | Lyy = 384932.49 | Lyz = -51946.31
 | Lzx = -39900.58 | Lzy = -51946.31 | Lzz = 100665.93
Moments of inertia: ( grams * square millimeters )
Taken at the output coordinate system.
 | Ixx = 1496094.97 | Ixy = -17996.70 | Ixz = 233171.33
 | Iyx = -17996.70 | Iyy = 1604720.43 | Iyz = -206488.57
 | Izx = 233171.33 | Izy = -206488.57 | Izz = 185887.67

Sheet: ForeArmMotor
Mass properties of Robot
Configuration: Default
Coordinate system: -- default --
Mass = 52.42 grams
Volume = 49683.44 cubic millimeters
Surface area = 31068.19 square millimeters
Center of mass: ( millimeters )
 | X = -0.01
 | Y = 12.86
 | Z = -75.20
Principal axes of inertia and principal moments of inertia: ( grams * square millimeters )
Taken at the center of mass.
 | Ix = ( 0.00, -0.23, 0.97) | Px = 11790.92
 | Iy = ( 0.04, -0.97, -0.23) | Py = 94991.62
 | Iz = ( 1.00, 0.04, 0.01) | Pz = 95348.49
Moments of inertia: ( grams * square millimeters )
Taken at the center of mass and aligned with the output coordinate system.
 | Lxx = 95347.94 | Lxy = -13.10 | Lxz = -5.23
 | Lyx = -13.10 | Lyy = 90654.04 | Lyz = -18496.44
 | Lzx = -5.23 | Lzy = -18496.44 | Lzz = 16129.04
Moments of inertia: ( grams * square millimeters )
Taken at the output coordinate system.
 | Ixx = 400510.75 | Ixy = -19.43 | Ixz = 31.81
 | Iyx = -19.43 | Iyy = 387149.29 | Iyz = -69190.53
 | Izx = 31.81 | Izy = -69190.53 | Izz = 24796.61

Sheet: GripperMotor
Mass properties of Robot
Configuration: Default
Coordinate system: -- default --
Mass = 23.88 grams
Volume = 22660.99 cubic millimeters
Surface area = 17185.76 square millimeters
Center of mass: ( millimeters )
 | X = -0.01
 | Y = 17.44
 | Z = -16.94
Principal axes of inertia and principal moments of inertia: ( grams * square millimeters )
Taken at the center of mass.
 | Ix = ( 1.00, -0.01, 0.00) | Px = 7302.66
 | Iy = ( 0.01, 0.61, -0.79) | Py = 8459.94
 | Iz = ( 0.01, 0.79, 0.61) | Pz = 10744.91
Moments of inertia: ( grams * square millimeters )
Taken at the center of mass and aligned with the output coordinate system.
 | Lxx = 7302.85 | Lxy = -20.33 | Lxz = -2.07
 | Lyx = -20.33 | Lyy = 9896.73 | Lyz = -1103.91
 | Lzx = -2.07 | Lzy = -1103.91 | Lzz = 9307.92
Moments of inertia: ( grams * square millimeters )
Taken at the output coordinate system.
 | Ixx = 21422.46 | Ixy = -23.63 | Ixz = 1.14
 | Iyx = -23.63 | Iyy = 16750.34 | Iyz = -8160.70
 | Izx = 1.14 | Izy = -8160.70 | Izz = 16573.93

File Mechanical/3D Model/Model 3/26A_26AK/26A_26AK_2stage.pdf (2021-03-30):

Wenn Sie diesen Text sehen, stellen Sie bitte

"Kommentare und Fomulare" im Drucken Dialog

auf "Dokument und Markierungen"

Explosion / Teile bewegen

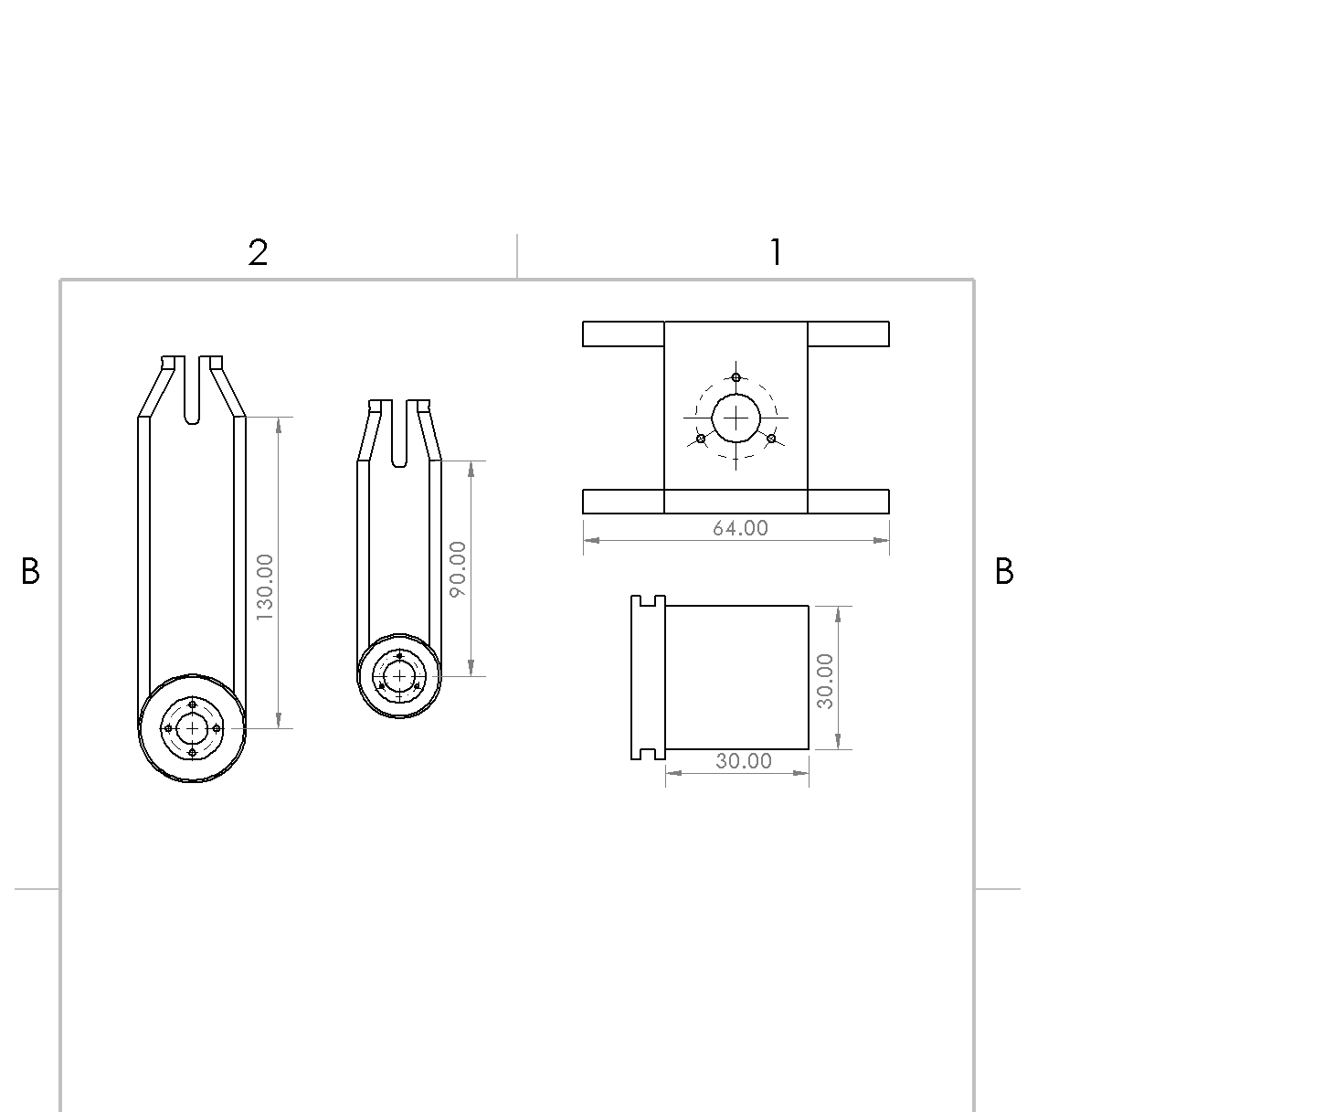
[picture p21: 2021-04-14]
Mechanical/3D Model/Model 4/RobotDrawing.JPG

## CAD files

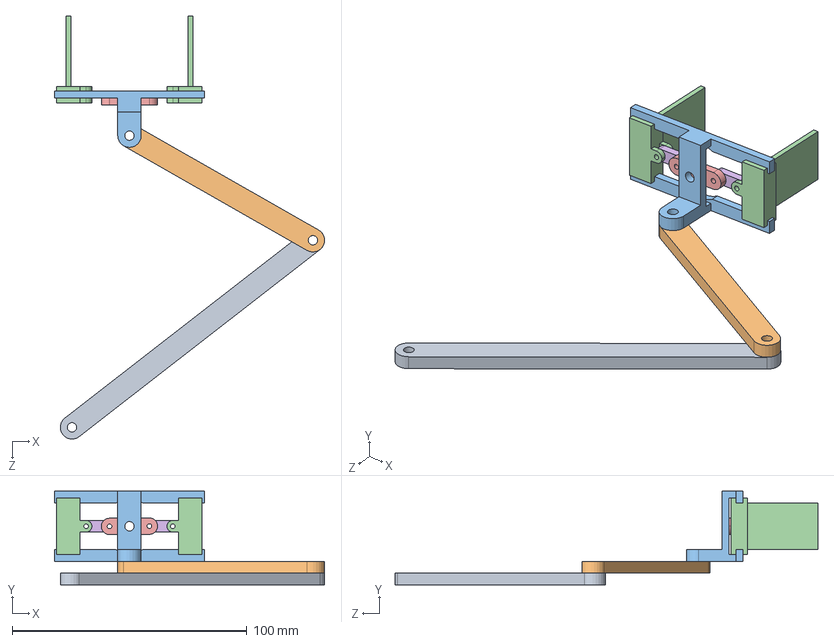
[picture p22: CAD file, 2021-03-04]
Mechanical/3D Model/Model 1/Robot.SLDASM
115.2 x 40.0 x 180.3 mm
BaseArmSegment^Robot
ForeArmSegment^Robot
Gripper^Robot
Claw^Robot x 2
PincherPivot^Robot
TurnBuckle^Robot x 2

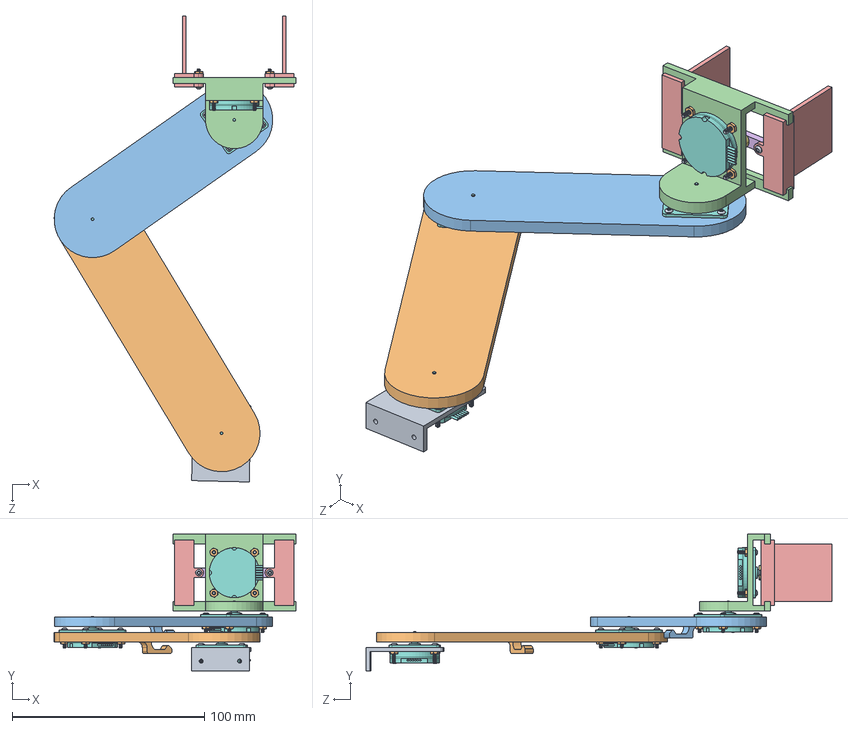
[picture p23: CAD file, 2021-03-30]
Mechanical/3D Model/Model 2/Robot.SLDASM
125.7 x 71.0 x 242.4 mm
MountingPlate^Robot
BaseArmSegment^Robot
ForeArmSegment^Robot
Gripper^Robot
Claw^Robot x 2
TurnBuckle^Robot x 2
PincherPivot^Robot
Motor_withplate_2607T_SR_IE2-16_3697.stp x 4
92949A889_18-8 SS BUTTON HEAD HEX DRIVE SCREW x 18
90480A036_LOW-STRENGTH STEEL HEX NUT x 18

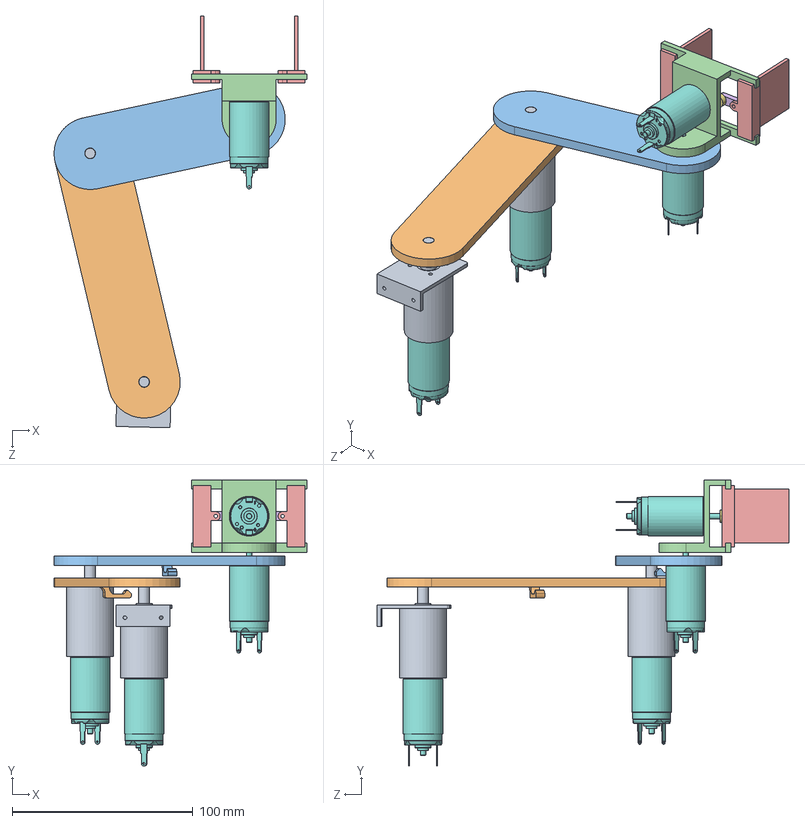
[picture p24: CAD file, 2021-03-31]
Mechanical/3D Model/Model 3/Robot.SLDASM
140.0 x 158.3 x 227.8 mm
MountingPlate^Robot
BaseArmSegment^Robot
ForeArmSegment^Robot
Gripper^Robot
Claw^Robot x 2
TurnBuckle^Robot x 2
PincherPivot^Robot
2237S_CXR.stp x 4
26A_26AK_3stage.stp x 2

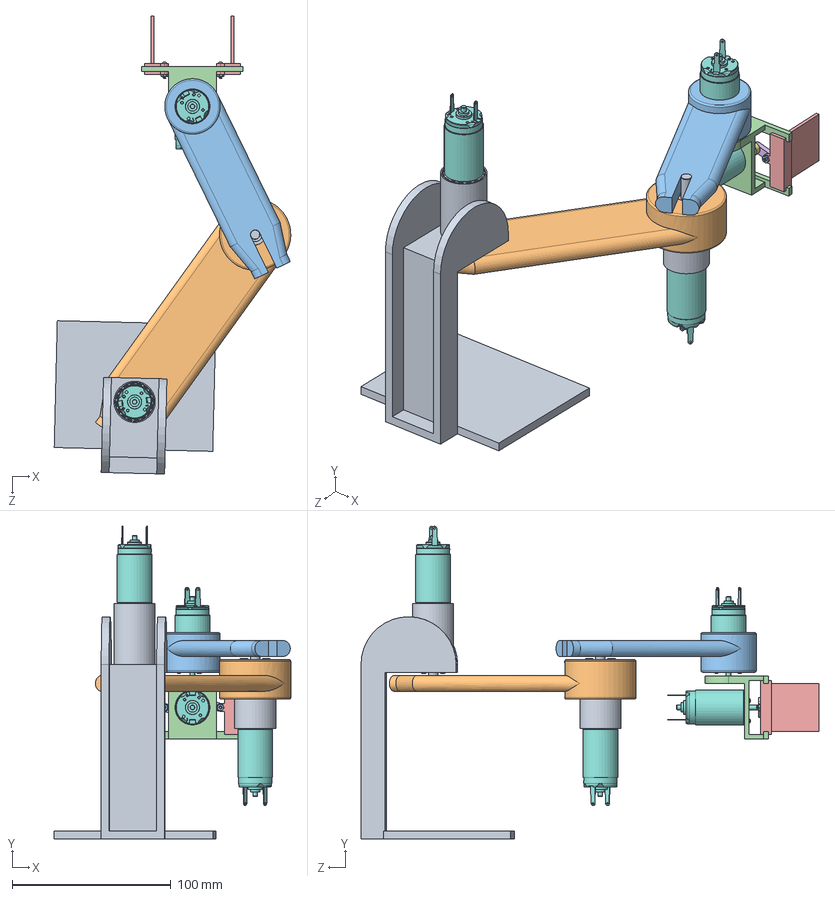
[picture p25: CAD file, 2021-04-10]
Mechanical/3D Model/Model 4/Robot.SLDASM
149.2 x 197.1 x 288.8 mm
MountingStand^Robot
BaseArmSegment^Robot
ForeArmSegment^Robot
Gripper^Robot
Claw^Robot x 2
TurnBuckle^Robot x 2
PincherPivot^Robot
2237S_CXR.stp x 4
26A_26AK_3stage.stp x 2
92949A889_18-8 SS BUTTON HEAD HEX DRIVE SCREW x 2
90480A036_LOW-STRENGTH STEEL HEX NUT x 2
92949A052_18-8 SS BUTTON HEAD HEX DRIVE SCREW x 6
92949A316_18-8 SS BUTTON HEAD HEX DRIVE SCREW x 8

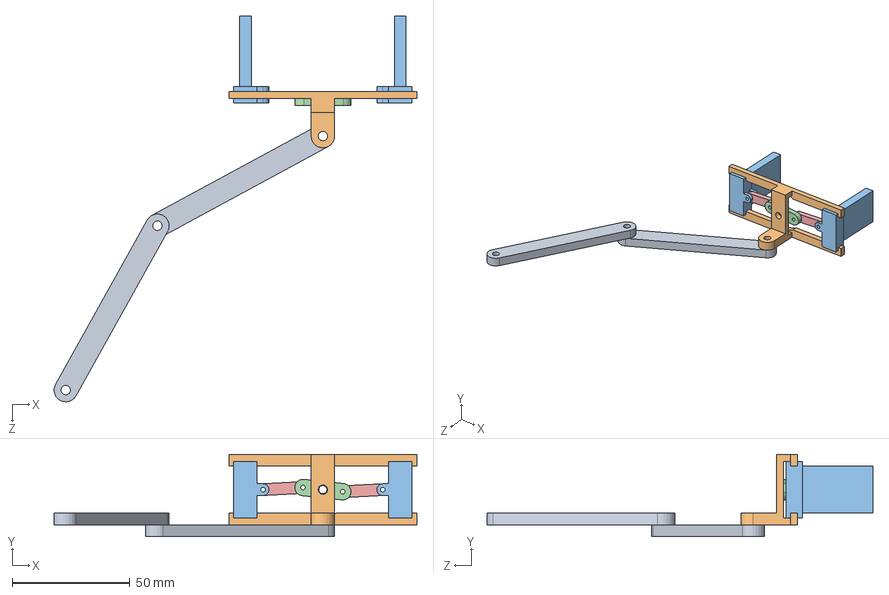
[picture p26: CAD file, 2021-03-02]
Mechanical/3D Model/Model 1/Robot_SimulationTesting.SLDASM
154.3 x 35.0 x 164.0 mm
ArmSegment^Robot_SimulationTesting x 2
Gripper^Robot_SimulationTesting
Claw^Robot_SimulationTesting x 2
GripperPivot^Robot_SimulationTesting
TurnBuckle^Robot_SimulationTesting x 2

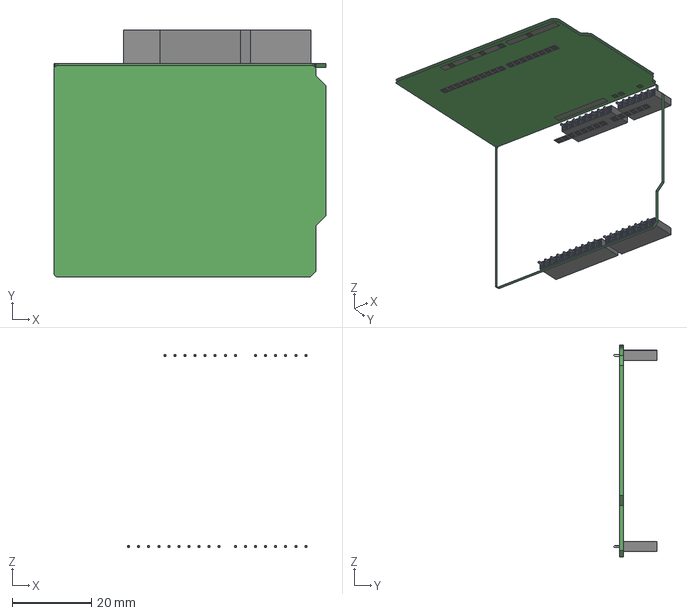
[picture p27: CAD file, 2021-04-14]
Electrical/Untitled - 3D.igs
68.6 x 62.3 x 53.8 mm

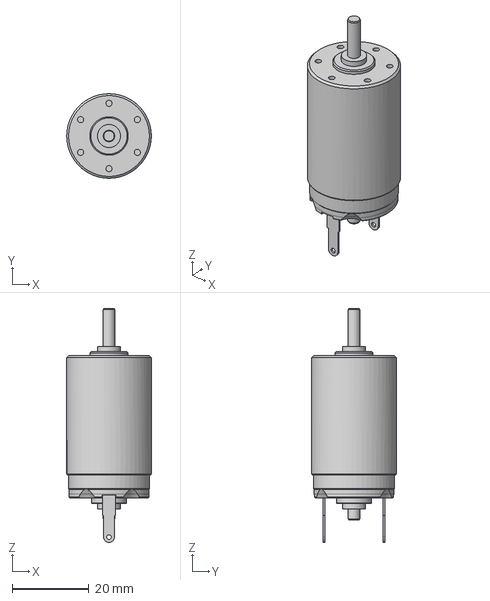
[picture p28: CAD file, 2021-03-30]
Mechanical/3D Model/Model 3/2237S_CXR/2237S_CXR.stp
22.0 x 22.0 x 60.8 mm

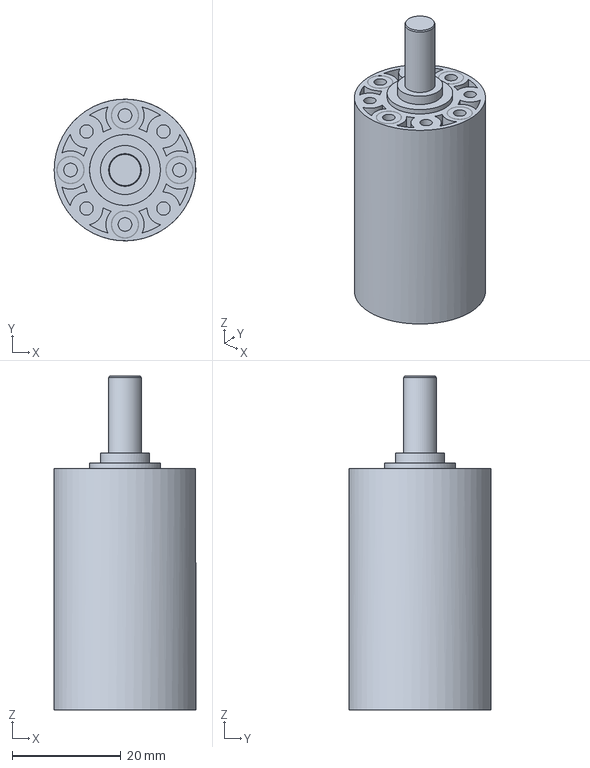
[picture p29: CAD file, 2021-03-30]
Mechanical/3D Model/Model 3/26A_26AK/26A_26AK_4stage.stp
26.0 x 26.0 x 61.3 mm

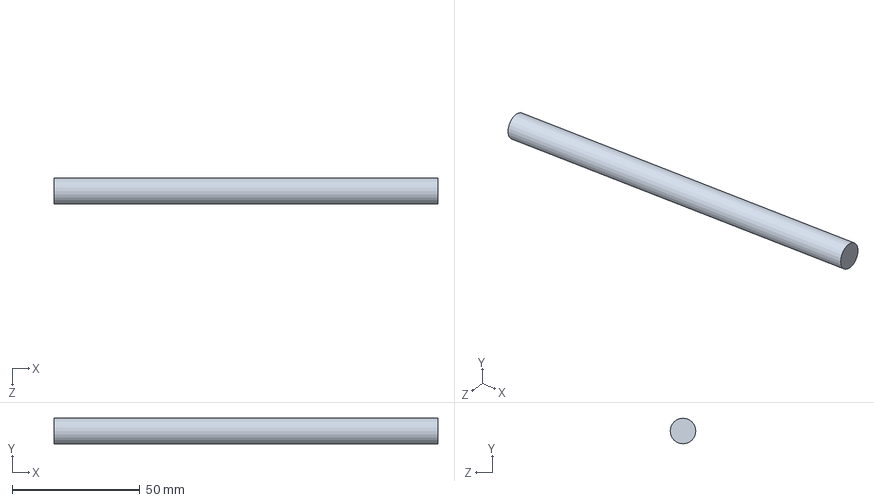
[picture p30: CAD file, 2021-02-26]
Control/ArmTesting.SLDPRT
150.0 x 10.0 x 10.0 mm

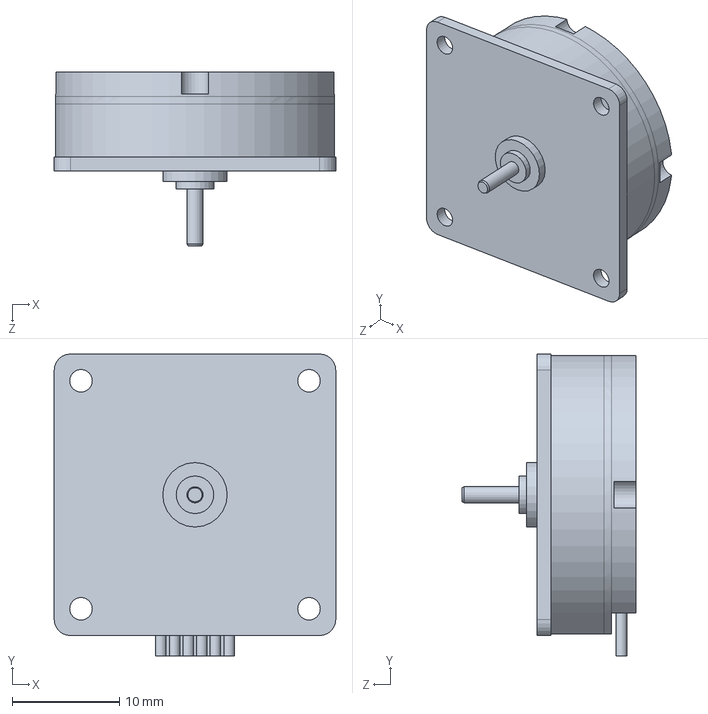
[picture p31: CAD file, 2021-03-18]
Mechanical/3D Model/Model 2/Motor_withplate_2607T_SR_IE2-16_3697.stp.SLDPRT
26.2 x 28.1 x 16.2 mm

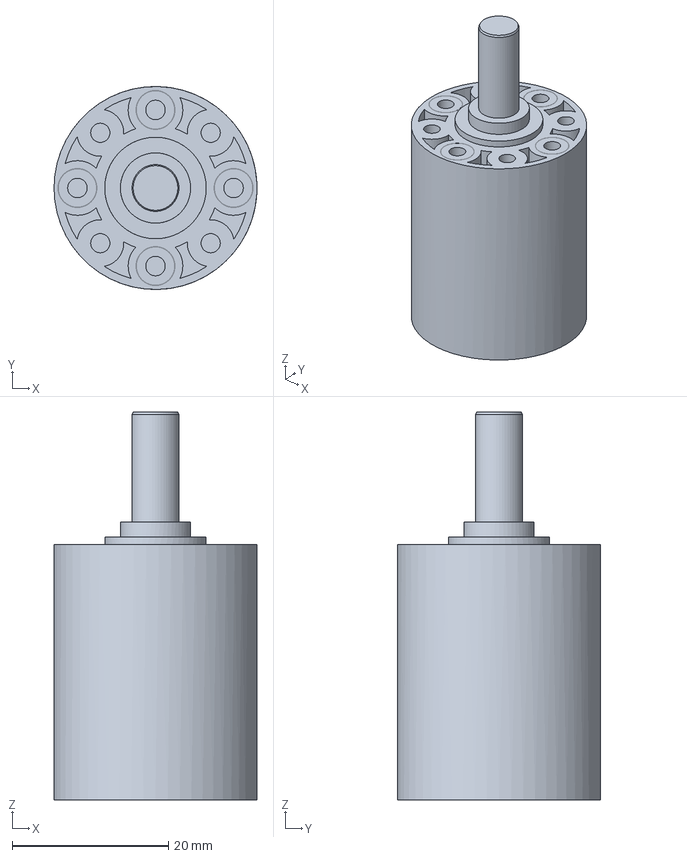
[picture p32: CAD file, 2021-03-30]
Mechanical/3D Model/Model 3/26A_26AK/26A_26AK_2stage.stp
26.0 x 26.0 x 49.7 mm

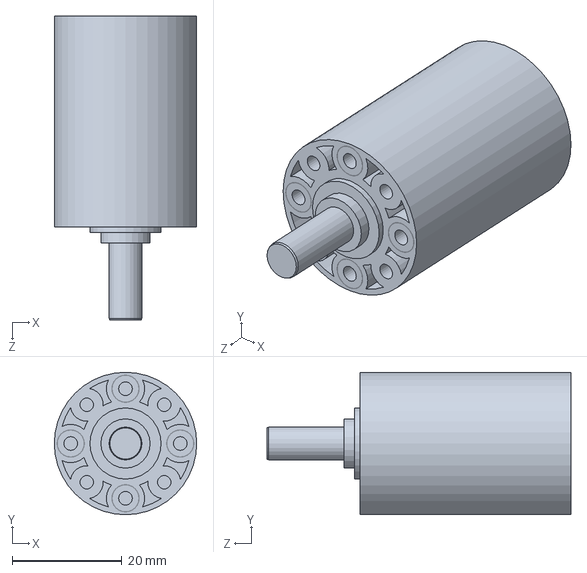
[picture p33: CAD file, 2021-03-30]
Mechanical/3D Model/Model 4/26A_26AK_3stage.stp.SLDPRT
26.0 x 26.0 x 55.5 mm

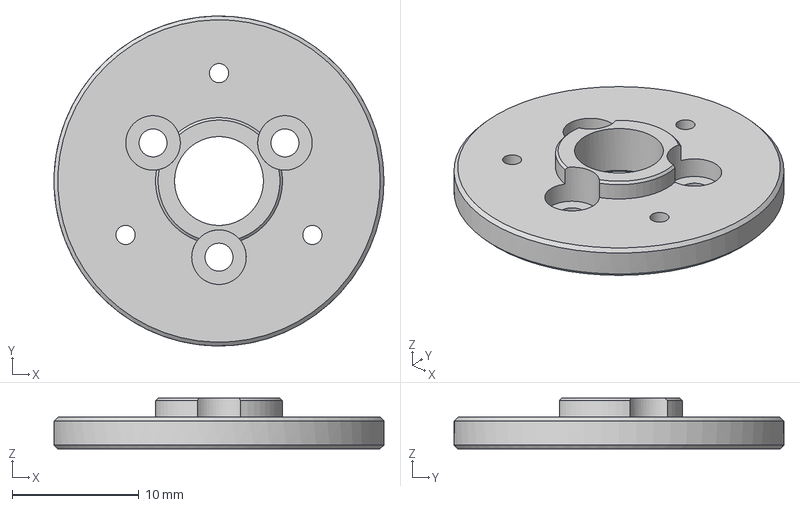
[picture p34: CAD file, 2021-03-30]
Mechanical/3D Model/Model 3/26A_26AK/26A_26AK_flange_a.stp
26.0 x 26.0 x 4.00 mm

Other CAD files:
Control/PathPlanning.SLDPRT
Mechanical/3D Model/Model 3/2237S_CXR.stp.SLDPRT
Control/PathPlanning.SLDDRW
Mechanical/3D Model/Model 3/2237S_CXR/2237S_CXR.igs
Mechanical/3D Model/Model 3/2237S_CXR/2237S_CXR.x_t
Mechanical/3D Model/Model 3/26A_26AK/26A_26AK_2stage.x_t
Mechanical/3D Model/Model 3/26A_26AK/26A_26AK_3stage.stp
Mechanical/3D Model/Model 3/26A_26AK/26A_26AK_3stage.x_t
Mechanical/3D Model/Model 3/26A_26AK/26A_26AK_4stage.x_t
Mechanical/3D Model/Model 3/26A_26AK/26A_26AK_flange_a.x_t
Mechanical/3D Model/Model 4/2237S_CXR.stp.SLDPRT
Mechanical/3D Model/Model 4/2237S_CXR/2237S_CXR.igs
Mechanical/3D Model/Model 4/2237S_CXR/2237S_CXR.x_t
Mechanical/3D Model/Model 4/26A_26AK/26A_26AK_2stage.x_t
Mechanical/3D Model/Model 4/26A_26AK/26A_26AK_3stage.stp
Mechanical/3D Model/Model 4/26A_26AK/26A_26AK_3stage.x_t
Mechanical/3D Model/Model 4/26A_26AK/26A_26AK_4stage.x_t
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

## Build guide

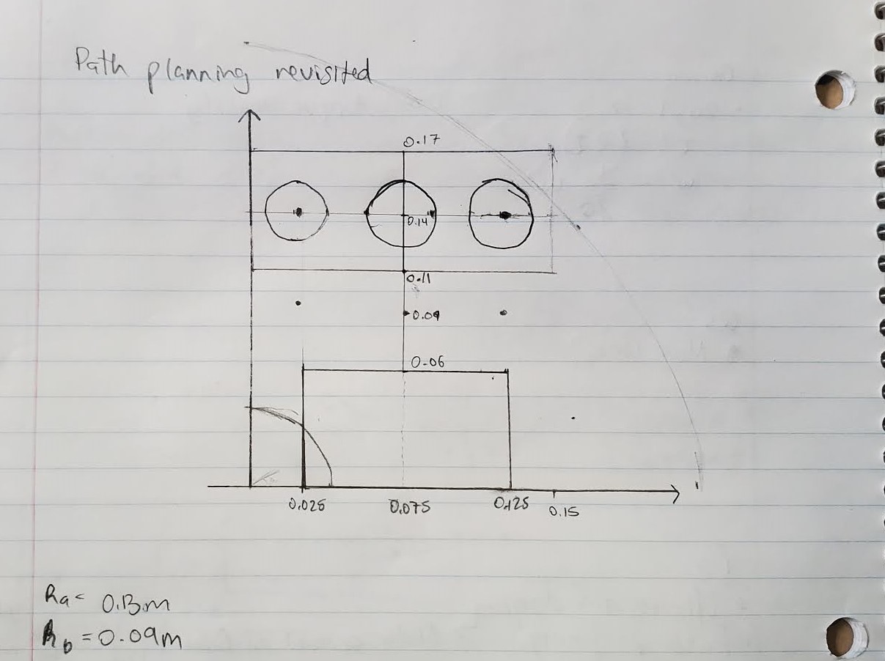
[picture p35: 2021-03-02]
Outline/Assembly_Line1.1.jpg

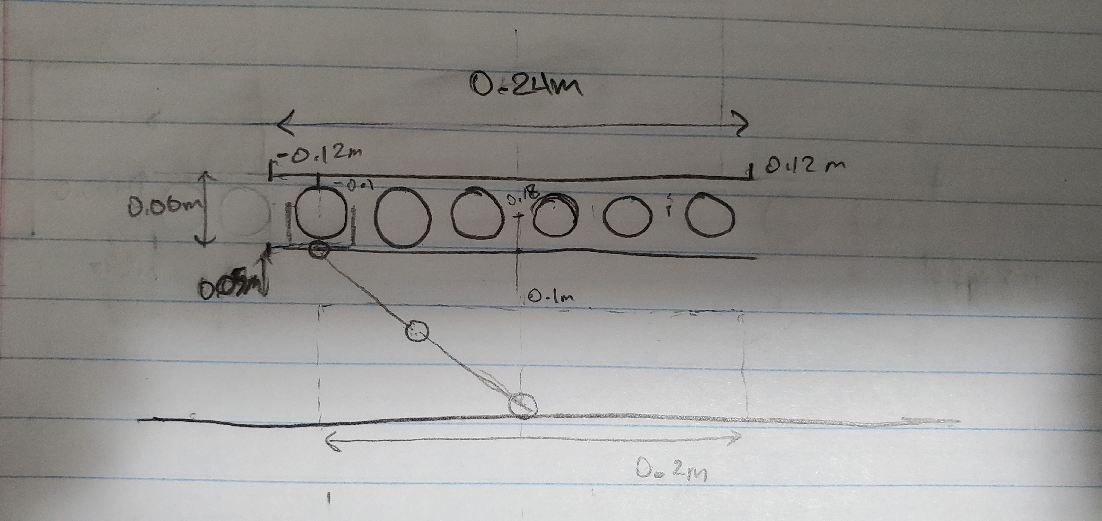
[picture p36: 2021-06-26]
Outline/Assembly_Line.jpg

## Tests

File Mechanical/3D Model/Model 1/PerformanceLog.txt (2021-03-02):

Number of Contacts: 21
Number of contact data: 1865

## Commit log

2021-02-26 Matlab dynamics
    [ArmTesting.SLDPRT]
2021-02-27 Create Arm Segment.SLDPRT
    [Arm Segment.SLDPRT]
2021-03-06 Simulation time!
    [Robot_SimulationTesting.SLDASM]
2021-03-07 Matlab Filtered derivative initial
2021-03-09 Derivative filter, filter, and integrator matlab functions implemented
2021-03-16 Arduino controller initial
2021-03-18 Create Drivers
2021-03-18 Solidwork model with motors and displacement tests
    [Motor_withplate_2607T_SR_IE2-16_3697.stp.SLDPRT, Motor_wo_plate.SLDPRT, Robot.SLDASM]
2021-03-18 Motor/encoder Datasheet
2021-03-18 Motor Driver with nominal motor
2021-03-22 Modified Motor Model
    [Mass Analysis.xlsx, Motor_withplate_2607T_SR_IE2-16_3697.stp.SLDPRT, Robot.SLDASM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]
2021-03-23 Matlab PID function implementation and debugging
2021-03-24 Added Fasteners to 3D Model
    [90480A036_LOW-STRENGTH STEEL HEX NUT.SLDPRT, 92949A889_18-8 SS BUTTON HEAD HEX DRIVE SCREW.SLDPRT, Robot.SLDASM]
2021-03-25 Updated SimX and Solidworks Models
    [Gripper.STL, Mass Analysis.xlsx, PincherPivot.STL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]
2021-03-30 Updated 3D Model with New Motor and Gearheads
    [2237S_CXR.igs, 2237S_CXR.stp, 2237S_CXR.stp.SLDPRT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]
2021-03-30 Model 3 - 3D Model and Mass Data
    [Mass Analysis.xlsx, Robot.SLDASM]
2021-03-31 Model 4 - The BeefCake
    Beefier arms and inverted gripper attachment
    [2237S_CXR.igs, 2237S_CXR.stp, 2237S_CXR.stp.SLDPRT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]
2021-03-31 Updated SimX
    [Gripper.STL, Mass Analysis.xlsx, PincherPivot.STL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]
2021-04-01 Marshmellows in SimX
    spaced at 35mm to avoid collision
2021-04-03 Simx adjusments, matlab controller finalized, Arduino controller completed
2021-04-04 SimX Pincher Implementation
    SimX simulation: for the Pincher model (Mechanical/Pincher/Pincher.isx), there is a Singular warning, however the model still functions.
    [Claw.STL, Gripper.STL, PincherPivot.STL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]
2021-04-05 better Pincher SimX model
    pincher in full model doesn't work
    [2237S_CXR.igs, 2237S_CXR.stp, 2237S_CXR.stp.SLDPRT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]
2021-04-05 mechanical folder fix
    accidentally deleted some stuff
    [2237S_CXR.igs, 2237S_CXR.stp, 2237S_CXR.stp.SLDPRT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]
2021-04-10 updated Solidworks model
    still need fasteners to attach arm segments
    [90480A036_LOW-STRENGTH STEEL HEX NUT.SLDPRT, 92949A052_18-8 SS BUTTON HEAD HEX DRIVE SCREW.SLDPRT, 92949A316_18-8 SS BUTTON HEAD HEX DRIVE SCREW.SLDPRT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]
2021-04-10 3D model updates
    just need to finish base (PCB enclosure & base motor mount)
    [90480A003_LOW-STRENGTH STEEL HEX NUT.SLDPRT, 91251A501_BLACK-OXIDE ALLOY STEEL SOCKET HEAD CAP SCREW.SLDPRT]
2021-04-11 Updated control report. Pathplan diagram
    [PathPlanning.SLDDRW, PathPlanning.SLDPRT]
2021-04-14 Demo video
    [PathPlanning.SLDPRT]
2021-04-14 Control report
    [PathPlanning.SLDDRW, PathPlanning.SLDPRT]
2021-04-14 Finished Mech Report
    [RobotDrawing.SLDDRW]
2021-06-26 PCB picture
